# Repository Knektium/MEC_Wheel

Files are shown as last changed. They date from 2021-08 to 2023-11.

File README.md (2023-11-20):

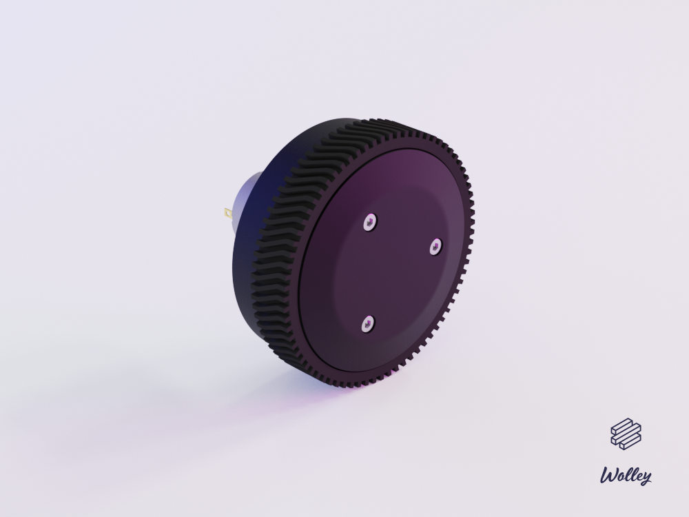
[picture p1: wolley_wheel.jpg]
Wolley Wheel


The Mechanical Project for the Wolley Wheel Module
==================================================

A robot wheel with built-in 2-stage planetary gearbox, motor and controller.

| Specification | |
| --- | ----:|
| Stage 1 ratio | 9.33 |
| Stage 2 ratio |  5.5 |
| Total ratio | 51.3 |

Parts
-----

### 3D Printable

| Qty | Part | Material | Part Number |
| ---:| --- | --- | ---:|
| 1 | Enclosure | ABS, PET-G or PLA* | 100116 |
| 1 | Back | PET-G | 100117 |
| 1 | Middle | PAHT-CF15 or PLA* | 100119 |
| 1 | Carrier | PET-G | 100122 |
| 3 | PlanetGearA | PET-G or PLA* | 100103 |
| 3 | PlanetGearB | PET-G or PLA* | 100107 |
| 1 | RingGearA | PET-G or PLA* | 100102 |
| 1 | Wheel | PET-G | 100106 |
| 1 | SunGearA | PET-G | 100118 |
| 1 | SunGearB | PET-G or PLA* | 100108 |
| 1 | Front | PAHT-CF15, PET-G, ABS or PLA* | 100120 |

_* HTPLA, Tough PLA, PLA+ or PLA with carbon fiber_

### Other Parts

| Qty | Part |
| ---:| --- |
| 4 | Socket Screw ISO 4762, M3 x 15 mm |
| 6 | Socket Screw ISO 4762, M3 x 4 mm |
| 2 | Socket Screw ISO 4762, M2.5 x 6 mm |
| 1 | Hex Stand-off, M3 x 11 mm (Ettinger 05.03.111) |
| 3 | Round Stand-off, M3 x 4 mm, Ø4.76 mm (Harwin R30-5000402) |
| 4 | Threaded Insert, M3 (Ruthex RX-M3x5.7) |
| 3 | Neodym Magnet, 2 x 4 mm (ex. Meder NdFeB N35) |
| 1 | DC Motor (ex. Mabuchi RS-385PV-2465) |
| 1 | Wolley MotorECU (100135) |

How to Build
------------

1. Print all parts without cogs with 0.25 mm layer height or thinner.
2. Print all other parts with 0.20 mm layer height or thinner.
3. Sandpaper all parts slightly and make sure they were printed as intended.
   This might not be needed at all for the parts printed in PET-G.
4. Assemble the motor, _MotorECU_ and _Back_.
5. Glue _SunGearA_ on the motor shaft using Loctite 648 and the mount tool.
6. Assemble the rest according to the explosion drawing. 
7. Make sure it is functional by rotating the wheel by hand. If it does not
   work, more sandpaping or better printing may be neccessary.
8. Run the motor for a bit to make the gearbox smoother. This could also be
   done by hand.
9. Take it apart and lubricate the internal parts slightly with lithium grease.
10. Assemble it again and use Loctite thread lock for the M3x4mm screws for
    preventing them from loosening.

Release Notes
-------------

Version 1.2:
 - Replaced the MotorECU v1.3 with v1.4 (no changes).
 - Added more verified materials to the READMED file.

Version 1.1:
 - Improved _Enclosure_ that is circular, covers more and has threaded
   inserts for easier assembly.
 - Made adjustments to fit a Mabuchi RS-385PV motor.
 - Sturdier _Middle_.
 - Improved the _Tire_ with pattern with better grip.
 - Better fitting _Carrier_.

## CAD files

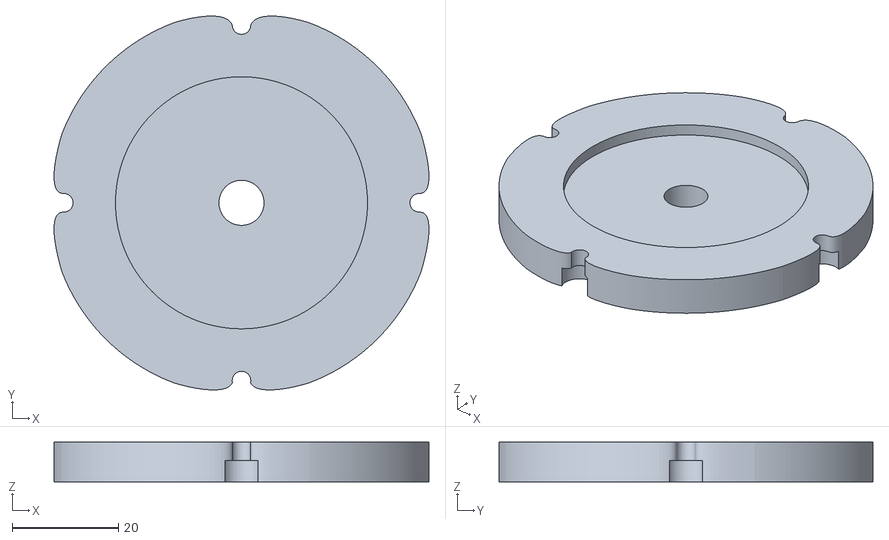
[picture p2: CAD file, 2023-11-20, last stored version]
Middle.stl
70.7 x 70.5 x 7.50

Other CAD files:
SpeedReducerWheel.dwg
Back.ipt
Carrier.ipt
CarrierB.ipt
Enclosure.ipt
Front.ipt
M3ThreadedInsert.ipt
Mabuchi_RS-385PV.ipt
Magnet.ipt
Magnet_CPY.ipt
Magnet_CPY1.ipt
Middle.ipt
MiddleStandoff.ipt
MotorPlate.ipt
Mount.ipt
PCB.ipt
PlanetGearA.ipt
PlanetGearA_CPY.ipt
PlanetGearA_CPY1.ipt
PlanetGearA_CPY2.ipt
PlanetGearA_CPY3.ipt
PlanetGearB.ipt
PlanetGearB_CPY.ipt
PlanetGearB_CPY1.ipt
RingGearA.ipt
Shaft1.ipt
Shaft1_1.ipt
Shaft2.ipt
SpeedReducerWheel.iam
SpeedReducerWheel.ipn
SpeedReducerWheel.ipt
SpeedReducerWheel/Design Accelerator/OldVersions/PlanetGearA_SpurGears2.0001.iam
SpeedReducerWheel/Design Accelerator/OldVersions/RingGearA_SpurGears.0001.iam
SpeedReducerWheel/Design Accelerator/OldVersions/SunGearA_SpurGears2.0001.iam
SpeedReducerWheel/Design Accelerator/PlanetGearA_SpurGears2.iam
SpeedReducerWheel/Design Accelerator/PlanetGearB_SpurGears1.iam
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

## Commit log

2021-03-08 Add the magnets and make sure the correct screws are shown in the drawings
    [Carrier.ipt, Magnet.ipt, Magnet_CPY.ipt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]
2021-07-15 Improve the inner gears
    [Mount.ipt, PlanetGearA_CPY.ipt, PlanetGearA_CPY1.ipt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]
2021-07-16 Improve the enclosure by making it circular and let it cover more
    [SpeedReducerWheel.ipn, SpeedReducerWheel.ipt]
2021-07-17 Make adjustments for another motor
    [SpeedReducerWheel.iam, SpeedReducerWheel.ipt]
2021-07-17 Improve the enclosure by making it smaller and closer to the wheel
    [SpeedReducerWheel.ipt]
2021-07-19 Improve the enclosure by adding threaded inserts
    [SpeedReducerWheel.ipt]
2021-07-21 Remove fillet from Front
    [SpeedReducerWheel.ipt]
2021-08-02 Make the Middle part sturdier by adding one mm to the mount holes
    [SpeedReducerWheel.ipt]
2021-08-05 Improve the size and pattern of the tire
    [SpeedReducerWheel.ipt]
2021-08-08 Set the enclosure diameter to 67.5 mm
    [SpeedReducerWheel.ipt]
2021-08-09 Update the assembly, presentation and drawing
    [Back.ipt, Carrier.ipt, CarrierB.ipt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]
2021-08-09 Rename to Wheel instead of SpeedReducerWheel
2021-08-09 Rename documents to Wolley Wheel instead of SpeedReducerWheel
    [SpeedReducerWheel.dwg, SpeedReducerWheel.iam, SpeedReducerWheel.ipt]
2021-08-13 Decrease the carrier radius by 0.25 mm to make it fit better
    [SpeedReducerWheel.ipt]
2021-08-13 Update assembly, presentation and drawings
    [Carrier.ipt, Magnet.ipt, Magnet_CPY.ipt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]
2021-08-13 Update the README file with better instructions and materials
2021-08-21 Increase the diameter of the carrier shafts
    [SpeedReducerWheel.ipt]
2021-08-21 Update the drawings and README file with part numbers
    [Back.ipt, Carrier.ipt, Enclosure.ipt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]
2021-08-21 Add company name to drawing
    [SpeedReducerWheel.dwg]
2021-08-29 Add the DC motor to the assembly and drawings
    [Mabuchi_RS-385PV.ipt, SpeedReducerWheel.dwg, SpeedReducerWheel.iam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]
2021-08-29 Update the picture with a one with the DC motor added
2023-11-20 Add models remade in Solvespace
    [Middle.stl]
2023-11-20 Remove Autodesk Inventor files
    [Back.ipt, Carrier.ipt, CarrierB.ipt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]
2023-11-23 Fix incorrect hex hole size
